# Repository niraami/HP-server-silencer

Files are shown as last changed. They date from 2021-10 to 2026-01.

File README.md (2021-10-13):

# HP server silencer

 

Inpired by the *many* other projects to silence the HP DL380e/p - but without most of the jank.  
Don't get me wrong, I love Arduino and projects that anyone can do themselves on a budget, but I just wanted something more robust. Something I could trust won't fail and somehow take the server with it. Something that is plug & play, and could be produced in bulk if needed (for relatively cheap).

I believe **this** is that something. The premise is quite simple. This STM32 equipped board acts as a middle man between the server & each fan. It takes the PWM signal from the server, scales & limits it to some user-configureable value and passes is along to the fan.

<div align="center">

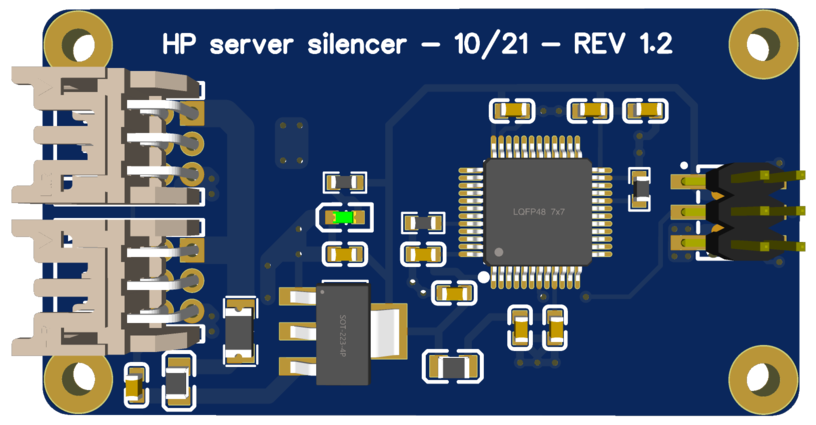
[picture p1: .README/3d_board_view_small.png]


</div>

# How it works
Here is a quick example of the boards fan curves in action. They are user configureable (i might even make a little configuration tool, so that you don't have to write configs manually.. if i feel motivated enough), but what you are seeing is the default curve that I've made as a good 'starting point'.  
I personally don't think it needs or should be changed, but I guess there are use cases where I can see both a *more* and *less* agressive curve make sense.

<div align="center">

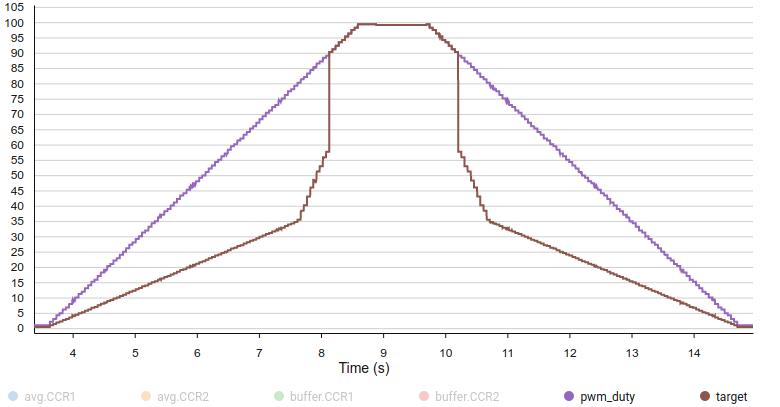
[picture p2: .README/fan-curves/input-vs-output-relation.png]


</div>

The **green curve is the input**. I've just got another STM32 producing a PWM signal @25kHz, that linearly sweeps the duty cycle from 0 to 100%, waits, and then back.  
The **red curve is the target** PWM. This is generated by the STM32 to control the fans.

Right now, you can manually configure the "fan curve" in [`curves.h`](src/Core/Src/curves.h).

Both of these values on the graph are after being smoothed/filtered via a rolling average. This average is produced by taking the last *n* samples (8 by default), or max. of last *t* milliseconds of data (400ms by default). What this means is that no data older than 400ms is taken into account for the average, and a maximum of last 8 values are.  
This technique gets rid of some of the signal uncertainty, but might not solve all of the issues that there are with scaling input values to different ranges - and also *maybe* introduces it's own artifacts, but none of those actually show up on my logic analyzer in a meaningful way, so it might just be issues with the STM32CubeMonitor polling rate or whatever.

Here are the values before any post processing is applied (on the left) and after (on the right).

<div align="center">

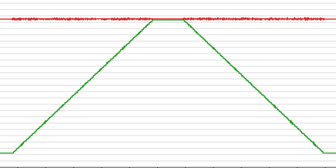
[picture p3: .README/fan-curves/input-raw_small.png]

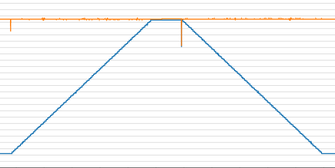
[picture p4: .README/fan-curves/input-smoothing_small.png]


</div>

# Design
All of the PCB design files can be found in the [pcb](pcb/) folder, but also on [OSHW](https://oshwlab.com/niraami/hp-server-silencer). 

I designed it from scratch in EasyEDA, and it has currently gone through 2 revisions. I've split them up using the EasyEDA versioning system, so you can check them out if, for whatever reason, you'd want...

The design is quite simple, as it just consists of 2 JST PHD 2.0 connectors, some power circuity, a STM32F103 (like in the bluepill) and a debugging header. All of the logic processing is done by the MCU, which is even more simplified by it's powerful PWM input & output capabilities. There are some quirks, but at least I didn't have to deal with counting the pulses myself or something.

To power the STM32, an AMS117-3.3 LDO piggibacks on the 12V coming from VCC - as the MCU requires literally milliamps of current, this shouldn't be an issue. I've chosen an LDO to simplify the programming & debugging, as it can also be powered off of 5V (from a USB port for example).

<div align="center">







</div>

## Fan PWM sense
The PWM Sense pins between the input & output connectors are connected - but it would be possible to reroute them, and use another STM32 timer to generate fake fan speed information for the server. The current server firmware version I've got doesn't seem to care about the reported speed much though, so I didn't implement that.

# Inspiration
Inspired by the many other HP fan "silencing" projects, but especially the [Max-Sum/HP-fan-proxy](https://github.com/Max-Sum/HP-fan-proxy) project. Though don't just blindly trust somebody's work, check it yourself... for example, I found that the the displayed [connector pinout](#motherboard-fan-pinout) doesn't match my server (and didn't check until the v1.0 of my board arrived :P).

These are just a *few* of the projects I came across while researching this topic. It seems that this series of server is quite notorious on [r/Homelab](https://www.reddit.com/r/homelab) for being so loud, people will try **literally** anything to make it shut up.
- [Silencing the HP Dl380, For Good.](https://www.reddit.com/r/homelab/comments/beuks5/silencing_the_hp_dl380_for_good/)
- [HP DL380p Arduino Fan Mod](https://www.reddit.com/r/homelab/comments/ny2eia/hp_dl380p_arduino_fan_mod_standby_question_and/)
- [Silence of the fans: Controlling HP server fans with a modified iLO4. And MORE!](https://www.reddit.com/r/homelab/comments/di3vrk/silence_of_the_fans_controlling_hp_server_fans/)
- [HP DL380P G8 fan noise with bios hack](https://www.reddit.com/r/homelab/comments/f94b0e/hp_dl380p_g8_fan_noise_with_bios_hack/)
- [Faking the fan signal on a DL380 G7](https://www.reddit.com/r/homelab/comments/72k3jf/faking_the_fan_signal_on_a_dl380_g7/)

# Sources
- [Max-Sum/HP-fan-proxy](https://github.com/Max-Sum/HP-fan-proxy)
- [STM32 Variable PWM Signal Output with timers, Keil Arm-mdk and Stm32cubemx ide](https://www.engineersgarage.com/stm32-variable-pwm-with-timers/)
- [Phil’s Lab - KiCad STM32 Hardware Design and JLCPCB Assembly](https://www.youtube.com/watch?v=t5phi3nT8OU)

# Part alternatives/not listed in BOM
- [50mm PHD2.0 JST cable (2x3P) - store 1](https://www.aliexpress.com/item/1005001346032672.html)
- [50mm PHD2.0 JST cable (2x3P) - store 2](https://www.aliexpress.com/item/1005002904897807.html)
- [JST PHD2.0 compatible 90˚ connector - alt 1](https://www.ebay.com/itm/PHD2-0-2-0mm-Pin-Header-PCB-Connector-Socket-Buckle-3-10P-Right-Angle-Various/153429645789)
- [JST PHD2.0 compatible 90˚ connector - alt 2](https://lcsc.com/product-detail/Wire-To-Board-Wire-To-Wire-Connector_HR-Joint-Tech-Elec-A2211WR-2X03P_C338851.html)
- [Tag-Connect - TC2030-IDC-NL-10](https://www.tag-connect.com/product/tc2030-idc-nl-10-6-pin-plug-of-nails-spring-pin-cable-with-0-1-ribbon-connector-10-version)
- [Tag-Connect - ARM20-CTX 20-Pin to TC2030-IDC Adapter for Cortex](https://www.tag-connect.com/product/arm20-ctx-20-pin-to-tc2030-idc-adapter-for-cortex)
- [USB connector to power the board while uploading firmware](https://www.aliexpress.com/item/4001198319430.html)

# Rants/stories

## Fan connectors
The connector type was very difficult to figure out, as it looks to be a proprietary 2.00mm pitch, 6 pin (2x3) keyed connector. And of course, HP will not just sell it to you, or even give you some datasheet for it.    
Luckily, Max's project was a very useful starting point, as Max found a compatible alternative, in the form of a JST PHD 2.0. Though, at first he wrote it to be a PH 2.0, but after much searching, I've found out that the D in PHD stands for "double row", and thus corrected him [here](https://github.com/Max-Sum/HP-fan-proxy/issues/4).

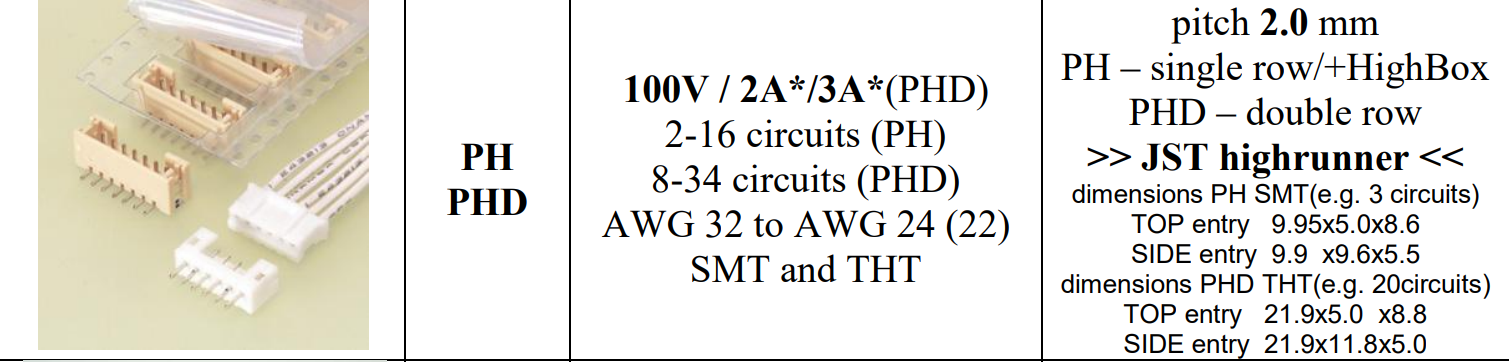
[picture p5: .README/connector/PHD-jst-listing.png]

The above screenshot is from a document which you can find [here](https://jst.de/uploads/product_overview/JST%20Product%20Overview_JD09.pdf) and a local copy at [docs/JST Product Overview_JD09.pdf](docs/JST%20Product%20Overview_JD09.pdf).

Not that just knowing the part number is going to do you much good.. it's a very rare one, barely anyone sells it, and crimping obscure JST's often requires special (and expensive) tools. But luck struck once again, and I managed to find a seller on AliExpress that has [super short PHD2.0](https://www.aliexpress.com/item/1005001346032672.html)'s in the 2x3 (6 pin) form!  
*In case that listing dissapears in the ether, here is at least the name:*  **5CM 26AWG 50MM PHD2.0 JST 2.0mm Pitch PHD PHDR-10VS 10 PIN Connector Wire Harness 2.0MM pitch 50MM double**

One more catch! I swear it's the last one ;)  
The connector doesn't fit into the header on the motherboard due to the small guides on the sides. But the plastic is soft enough, that with a steady hand and a sharp knife, they can be cut off really easily.

<div align="center">

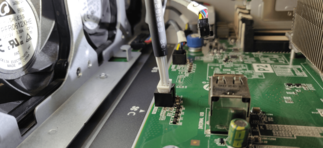
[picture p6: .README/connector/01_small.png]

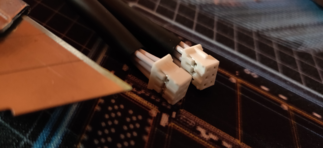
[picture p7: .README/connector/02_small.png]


</div>

## Motherboard fan pinout
Max's documentation provides a [very similar diagram](https://raw.githubusercontent.com/Max-Sum/HP-fan-proxy/master/images/post-8123-0-98784900-1394609613.png) to what I've got below, but we, for whatever reason, have the GND & NC pins swapped. There isn't even a cable there for me, so maybe there are some differences between server batches.. I've got no idea. So just in case, check what kind of a pinout your server has

Here is a "corrected" pinout, along with pictures of how the cable wires look (their colors do make a bit of sense):

<div align="center">

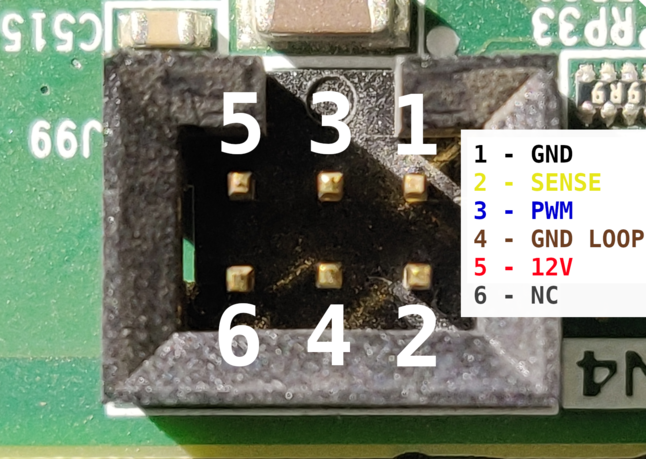
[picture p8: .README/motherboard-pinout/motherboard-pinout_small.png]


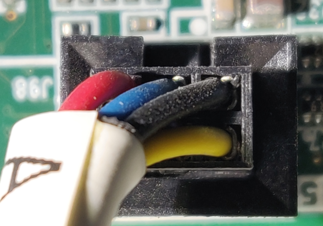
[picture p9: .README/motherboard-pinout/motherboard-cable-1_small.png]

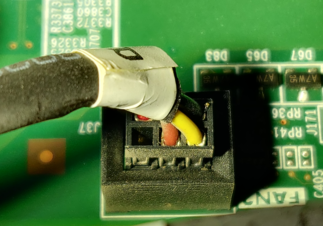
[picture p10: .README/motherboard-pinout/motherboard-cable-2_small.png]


</div>

## The server/fans use an inverted PWM signal
So yeah, I was very confused when plugging in my board that is meant to make the server more quiet, but instead it went full tilt. After a bit of headscratching, and using one of the prototype boards as a breakout, I figured out that what the ILO reports as 66%, is actually 33% duty cycle on the PWM.  
In STM32 terms, this is called PWM polarity, and should be set to `low`.

Luckily this required just 2 lines in the code to change, but nevertheless, it was quite funny.

<div align="center">

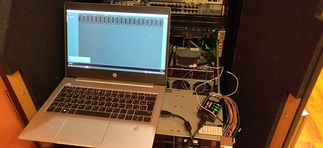
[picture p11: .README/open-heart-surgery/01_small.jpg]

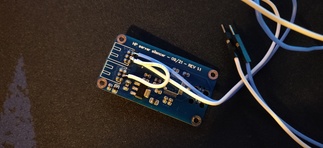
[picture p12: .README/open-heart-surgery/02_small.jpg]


</div>

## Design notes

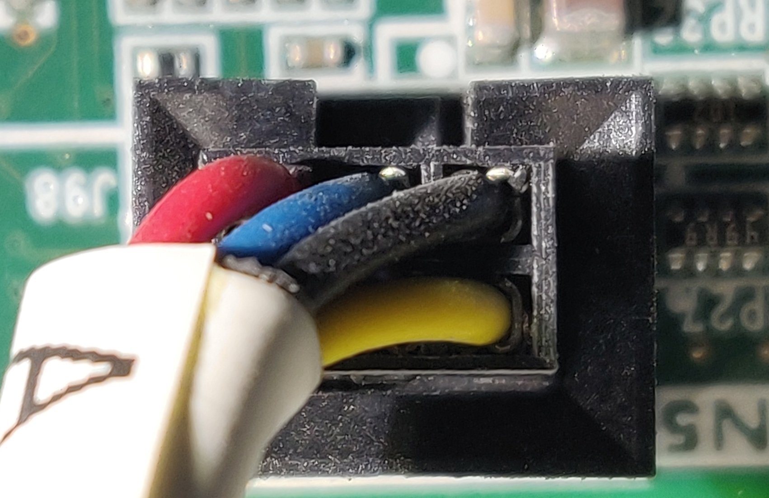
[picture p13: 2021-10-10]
.README/motherboard-pinout/motherboard-cable-1.png

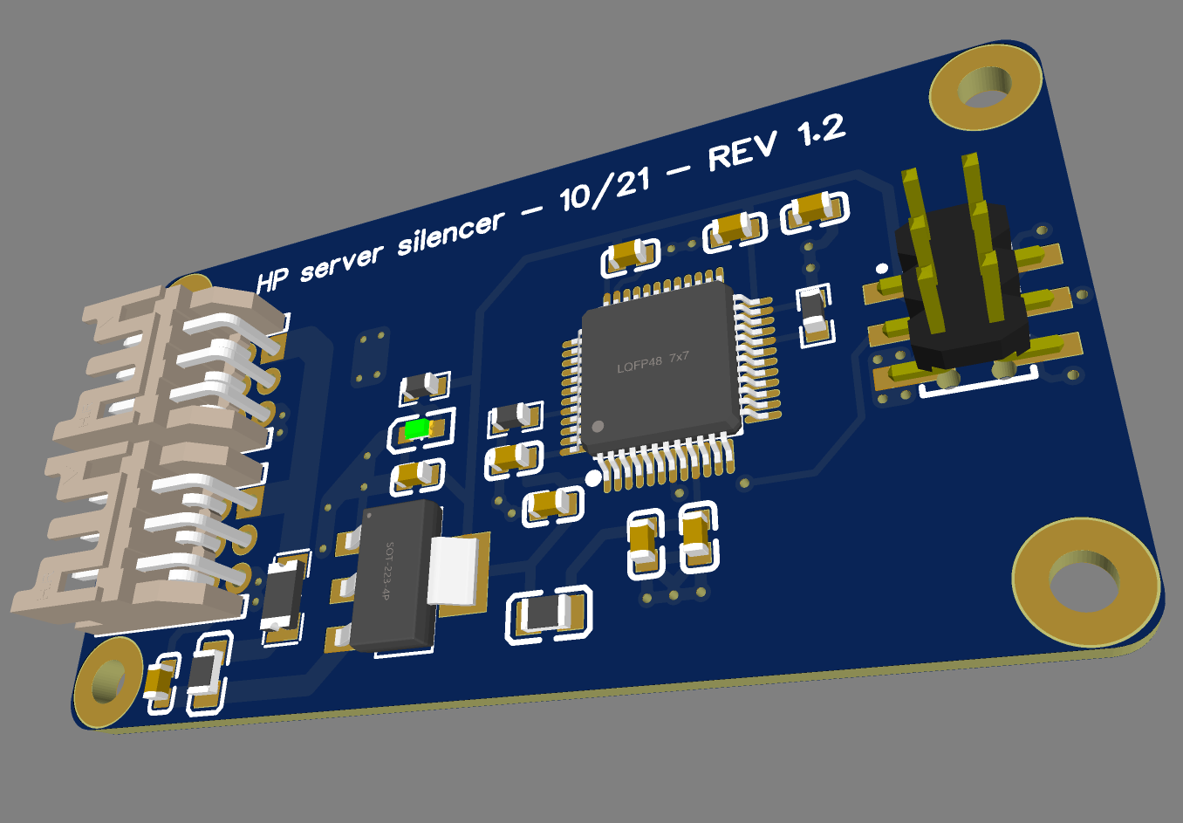
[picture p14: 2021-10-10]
.README/OSHW-thumbnail.png

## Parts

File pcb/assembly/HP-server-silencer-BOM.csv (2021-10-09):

ID | Name | Designator | Footprint | Quantity | Manufacturer Part | Manufacturer | Supplier | Supplier Part | Price
1 | TC2030-NL | P1 | TC2030-MCP-NL-JKA | 1
2 | PHD-2*3AW | J1,J2 | CONN-TH_A2004WR-2X03P | 2 | A2004WR-2X03P | HR(Joint Tech Elec) | LCSC | C476867 | 0.074
3 | STM32F103C8 | U3 | LQFP-48_L7.0-W7.0-P0.50-LS9.0-BL | 1 | STM32F103C8T6 | STMicroelectronics | LCSC | C8734 | 16.016
4 | SMD header | H1 | HDR-SMD_6P-P2.00-V-M-R2-C3-S2.0 | 1 | X4621WVS-2x03I-C40D64 | XKB Connectivity | LCSC | C917608 | 0.14
5 | Green | LED1 | LED0603-R-RD | 1 | 19-217/GHC-YR1S2/3T | EVERLIGHT | LCSC | C72043 | 0.025
6 | 180 | R3 | R0603 | 1 | 0603WAF1800T5E | UniOhm | LCSC | C22828 | 0.001
7 | 10uF | C1,C2,C12 | C0603 | 3 | CL10A106KP8NNNC | SAMSUNG | LCSC | C19702 | 0.007
8 | 350mA | F1 | F1206 | 1 | 1206L035YR | Littelfuse | LCSC | C99562 | 0.042
9 | 100 @ 100MHz | L1,L2 | L0805 | 2 | CBW201209U101T | FH | LCSC | C74487 | 0.005
10 | 10K | R1,R2 | R0603 | 2 | 0603WAF1002T5E | UniOhm | LCSC | C25804 | 0.001
11 | AMS1117-3.3 | U2 | SOT-223-3_L6.5-W3.4-P2.30-LS7.0-BR | 1 | AMS1117-3.3 | AMS | LCSC | C6186 | 0.17
12 | 100nF | C3,C5,C6,C7,C8 | C0603 | 5 | CC0603KRX7R9BB104 | YAGEO | LCSC | C14663 | 0.003
13 | 10nF | C4 | C0603 | 1 | 0603B103K500NT | FH(Guangdong Fenghua Advanced Tech) | LCSC | C57112 | 0.003

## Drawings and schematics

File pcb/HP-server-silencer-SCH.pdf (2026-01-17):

IO

## Power regulation

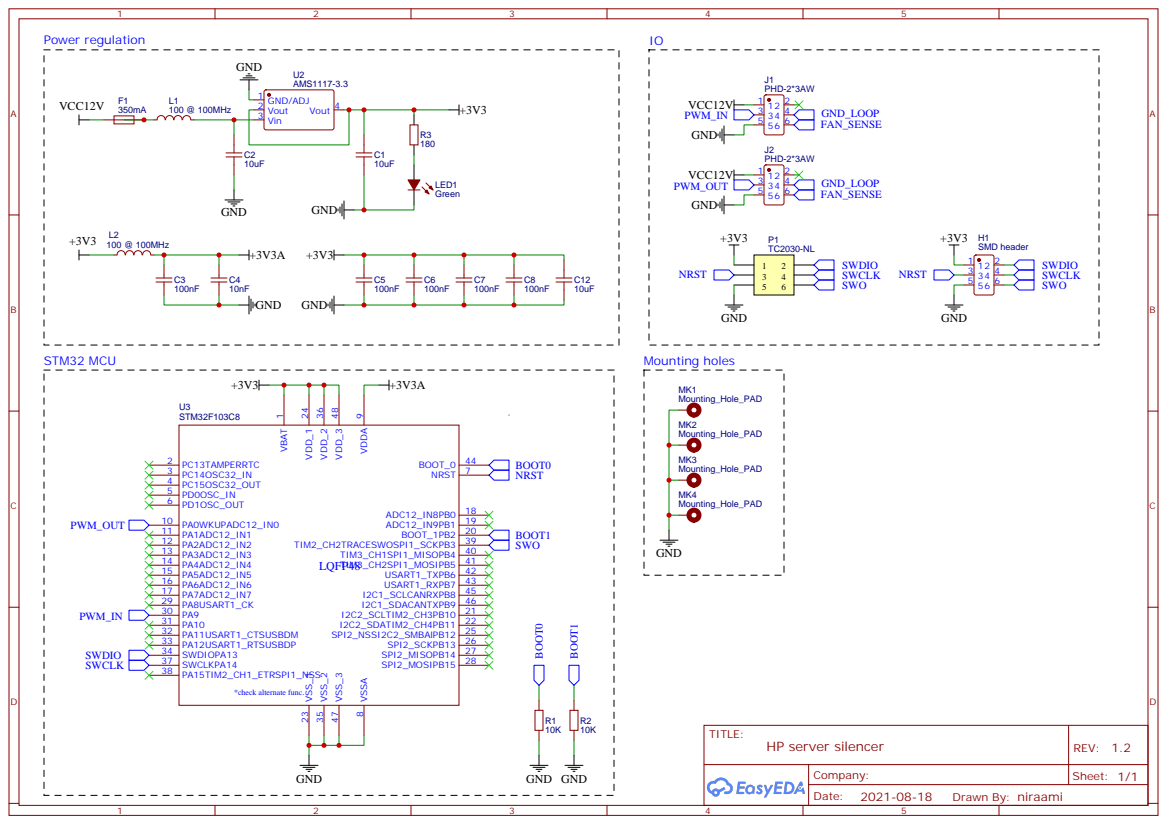
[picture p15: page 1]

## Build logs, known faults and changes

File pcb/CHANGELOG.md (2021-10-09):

(DD.MM.YYYY) - version

**19.08.2021 - v1.0**
Initial version

**11.09.2021 - v1.1**
*Complete redesign (of PCB, schematic mostly untouched)*
- input connectors are now on the same side to improve mounting in the server, as well as routing
- fixed completely incorrect input pinout
- fixed component spacing issues (gaps betwen caps were almost nonexistent)
- removed unnecessary silkscreen markings
- removed unnecessary decoupling caps
- replaced 3mm mounting holes /w 2mm

**07.10.2021 - v1.2**
*Minor fixes & improvements*
- fixed mirrored input connectors (GND flipped /w VCC, FAN_SENSE /w NC pin 2)
- replaced TC2050 /w TC2030-NL - less pins, no legs, etc
- added power indication LED
- added a SMD 2.5mm pitch pin header on top of the TC footprint (as an alternative)
- generally improved trace routing a bit (mostly optically & logically)

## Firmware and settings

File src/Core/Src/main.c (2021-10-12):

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
/* Includes ------------------------------------------------------------------*/
#include "main.h"
#include "cmsis_os.h"

/* USER CODE BEGIN Includes */
#include "curves.h"
/* USER CODE END Includes */

/* USER CODE BEGIN PD */

/**
 * Maximum number of messages that are pending from the TIM1 IRQ handler. This
 * buffer is used to handle bursts of messages from the IRQ - ex. when the PWM
 * signal is slowly changing.
 */
#define TIM1_IRQ_BUFFER_MAX_BACKLOG 4

/**
 * Maximum number of messages/events stored in the TIM1 IRQ buffer
 * This value directly affects how much smoothing is applied to the input signal
 * @note High values may lead to artifacts
 */
#define TIM1_IRQ_BUFFER_LENGTH 8

/**
 * Maximum lifespan of a buffer entry (in ms)
 * Specifies the maximum amount of time an entry is going to be counted into
 * the input average. After this time, the entry is guaranteed to be thrown
 * out. This might also happen much sooner if the interval at which the entries
 * are being added into the buffer is smaller than this value divided by the
 * buffer's length.
 * @note I recommend setting this value to be neatly divisible by the buffer's
 * length, otherwise rounding will take place anyways
 */
#define TIM1_IRQ_BUFFER_LIFESPAN 400

/**
 * This duty cycle is used on edge-cases where calculations fail or receive
 * invalid data
 * The default value is 100
 */
#define FAILSAFE_DUTY_CYCLE 100
/* USER CODE END PD */

TIM_HandleTypeDef htim1;
TIM_HandleTypeDef htim2;

/* Definitions for defaultTask */
osThreadId_t defaultTaskHandle;
const osThreadAttr_t defaultTask_attributes = {
  .name = "defaultTask",
  .stack_size = 128 * 4,
  .priority = (osPriority_t) osPriorityNormal1,
};
/* Definitions for inputFilter */
osThreadId_t inputFilterHandle;
const osThreadAttr_t inputFilter_attributes = {
  .name = "inputFilter",
  .stack_size = 128 * 4,
  .priority = (osPriority_t) osPriorityNormal,
};
/* USER CODE BEGIN PV */

/**
 * Message queue used to store reported CCR values from the TIM1_CC_IRQ handler
 */
MessageBufferHandle_t tim1_irq_backlog = NULL;
/**
 * A small buffer used to transfer the filtered signal from the input filter to
 * the main thread.
 */
MessageBufferHandle_t tim1_filtered_buffer = NULL;


/* USER CODE END PV */

void SystemClock_Config(void);
static void MX_GPIO_Init(void);
static void MX_TIM1_Init(void);
static void MX_TIM2_Init(void);
void StartDefaultTask(void *argument);
void InputFilterTask(void *argument);

/* USER CODE BEGIN 0 */

/**
 * @brief Sets the PWM duty cycle for the desired TIMER channel
 * @param htim Timer handle
 * @param channel PWM generation channel
 * @param duty_cycle Desired duty cycle in percent. Resolution is calculated
 * based on the period configured of the timer instance.
 */
static void setDutyCycle(TIM_HandleTypeDef* const htim,
    uint32_t channel, float duty_cycle)
{
  // Constrain the provided duty cycle to avoid undefined behaviour
  if (duty_cycle > 100) duty_cycle = 100;
  if (duty_cycle < 0) duty_cycle = 0;

  // Calculate the period resolution (1% of the period value)
  float pw_resolution = ((float)htim->Init.Period + 1.0f) / 100.0f;
  // Calculate & set the actual PWM period
  uint16_t pw_desired = pw_resolution * duty_cycle;
  __HAL_TIM_SET_COMPARE(htim, channel, pw_desired);
}

/* USER CODE END 0 */

/**
  * @brief  The application entry point.
  * @retval int
  */
int main(void)
{
  /* USER CODE BEGIN 1 */
  tim1_irq_backlog = xMessageBufferCreate(
    TIM1_IRQ_BUFFER_MAX_BACKLOG * (sizeof(CCRPair) + sizeof(size_t)) );
  tim1_filtered_buffer = xMessageBufferCreate(
    (sizeof(CCRPair) + sizeof(size_t)) );
  /**
   * Asserts will fail if there isn't sufficient FreeRTOS heap available for the
   * buffers to be created successfully.
   */
  assert_param(tim1_irq_backlog != NULL);
  assert_param(tim1_filtered_buffer != NULL);
  /* USER CODE END 1 */

  /* MCU Configuration--------------------------------------------------------*/

  /* Reset of all peripherals, Initializes the Flash interface and the Systick. */
  HAL_Init();

  /* Configure the system clock */
  SystemClock_Config();

  /* Initialize all configured peripherals */
  MX_GPIO_Init();
  MX_TIM1_Init();
  MX_TIM2_Init();
  /* USER CODE BEGIN 2 */

  // Start interrupts on TIM1 CH1 & CH2
  HAL_TIM_IC_Start_IT(&htim1, TIM_CHANNEL_1);
  HAL_TIM_IC_Start_IT(&htim1, TIM_CHANNEL_2);

  // Start PWM generation on TIM2 CH1
  HAL_TIM_PWM_Start(&htim2, TIM_CHANNEL_1);

  /**
   * Clear the TIM1 IRQ message queue, just in case anything got added during
   * initialization
   * @note This is mostly useful while using GDB for debugging
   */
  xMessageBufferReset(tim1_irq_backlog);

  /* USER CODE END 2 */

  /* Init scheduler */
  osKernelInitialize();

  /* USER CODE BEGIN RTOS_MUTEX */
  /* add mutexes, ... */
  /* USER CODE END RTOS_MUTEX */

  /* USER CODE BEGIN RTOS_SEMAPHORES */
  /* add semaphores, ... */
  /* USER CODE END RTOS_SEMAPHORES */

  /* USER CODE BEGIN RTOS_TIMERS */
  /* start timers, add new ones, ... */
  /* USER CODE END RTOS_TIMERS */

  /* USER CODE BEGIN RTOS_QUEUES */
  /* add queues, ... */
  /* USER CODE END RTOS_QUEUES */

  /* Create the thread(s) */
  /* creation of defaultTask */
  defaultTaskHandle = osThreadNew(StartDefaultTask, NULL, &defaultTask_attributes);

  /* creation of inputFilter */
  inputFilterHandle = osThreadNew(InputFilterTask, NULL, &inputFilter_attributes);

  /* USER CODE BEGIN RTOS_THREADS */
  /* add threads, ... */
  /* USER CODE END RTOS_THREADS */

  /* USER CODE BEGIN RTOS_EVENTS */
  /* add events, ... */
  /* USER CODE END RTOS_EVENTS */

  /* Start scheduler */
  osKernelStart();

  /* We should never get here as control is now taken by the scheduler */
  /* Infinite loop */
  /* USER CODE BEGIN WHILE */
  while (1)
  {
    /* USER CODE END WHILE */

    /* USER CODE BEGIN 3 */
  }
  /* USER CODE END 3 */
}

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
/* USER CODE BEGIN Header_StartDefaultTask */
/**
  * @brief  Function implementing the defaultTask thread.
  * @param  argument: Not used
  * @retval None
  */
/* USER CODE END Header_StartDefaultTask */
void StartDefaultTask(void *argument)
{
  /* USER CODE BEGIN 5 */
  CCRPair evt = { 0, 0 };

  /* Infinite loop */
  for(;;)
  {
    /** If > 0, we've received a message and it was stored to `evt` */
    size_t recv = xMessageBufferReceive(tim1_filtered_buffer,
      &evt, sizeof(evt), portMAX_DELAY);

    if (recv == 0) {
      // Continue waiting if the specified timeout expired
      continue;
    }

    /** Calculated input PWM frequency */
    uint32_t pwm_freq = HAL_RCC_GetSysClockFreq() / (TIM1->PSC + 1) / evt.CCR2;
    /** Ignore bogus input frequencies (outside of the PWM spec) */
    if (pwm_freq > 28000 || pwm_freq < 21000) {
      continue;
    }

    /** Calculated input PWM duty cycle as percentage */
    float pwm_duty = (evt.CCR2 - evt.CCR1) / (evt.CCR2 / 100.0f);
    // Invert the duty cycle, as it's polarity is reversed (low instead of high)
    pwm_duty = 100.0f - pwm_duty;

    // Find the first curve range that matches our input
    uint8_t n_curves = sizeof(k_curve) / sizeof(CurvePoint);

    for (uint8_t i = 0; i < n_curves; i++) {
      CurvePoint point = k_curve[i];

      if (point.in_start < pwm_duty && point.in_end > pwm_duty) {
        /** Target PWM duty cycle calculated based on the point's parameters */
        float target = point.out_start + (
          (point.out_end - point.out_start) * (pwm_duty - point.in_start) /
            (point.in_end - point.in_start)
        );

        setDutyCycle(&htim2, TIM_CHANNEL_1, target);

        break;
      }

      if (i + 1 == n_curves) {
        // Set failsafe duty cycle if no curve was found
        setDutyCycle(&htim2, TIM_CHANNEL_1, FAILSAFE_DUTY_CYCLE);
      }
    }
  }
  /* USER CODE END 5 */
}

/* USER CODE BEGIN Header_InputFilterTask */
/**
* @brief Function implementing the inputFilter thread.
* @param argument: Not used
* @retval None
*/
/* USER CODE END Header_InputFilterTask */
void InputFilterTask(void *argument)
{
  /* USER CODE BEGIN InputFilterTask */
  CCRPair data[TIM1_IRQ_BUFFER_LENGTH] = {0};
  CCRPair buffer = {0, 0};
  CCRPair sum = {0, 0};

  CCRPair* head_ptr = data;

  size_t recv = 0;
  size_t n_entries = 0;

  /** Used to optimize CPU cycles when no action is required */
  uint32_t cycle_ms = portMAX_DELAY;

  /* Infinite loop */
  for(;;)
  {
    // If > 0, we've received a message and it was stored to the buffer
    recv = xMessageBufferReceive(tim1_irq_backlog, &buffer,
      sizeof(CCRPair), cycle_ms);

    if (!recv && n_entries <= 1) {
      // Wait for a message indefinitely
      cycle_ms = portMAX_DELAY;

      continue;
    } else {
      cycle_ms = pdMS_TO_TICKS(
        TIM1_IRQ_BUFFER_LIFESPAN / TIM1_IRQ_BUFFER_LENGTH );
    }

    // Remove the entry that is about to get overwritten from the sum
    sum = (CCRPair) {
      sum.CCR1 - head_ptr->CCR1,
      sum.CCR2 - head_ptr->CCR2
    };

    if (!recv) {
      // Clear the current entry if no message was received
      *head_ptr = (CCRPair) {0, 0};
      // Decrement the number of available entries
      n_entries--;
    } else {
      // Append the new entry to the buffer & the rolling sum
      *head_ptr = buffer;

      sum = (CCRPair) {
        sum.CCR1 + head_ptr->CCR1,
        sum.CCR2 + head_ptr->CCR2
      };

      // Only increment the number of entries if the buffer isn't already full
      if (n_entries < TIM1_IRQ_BUFFER_LENGTH) {
        n_entries++;
      }
    }

    // Push the head_ptr address forward & check for bounds
    if (++head_ptr == &data[TIM1_IRQ_BUFFER_LENGTH]) {
      head_ptr = data;
    }

    // Send new input value to the main task
    CCRPair avg = {
      sum.CCR1 / n_entries,
      sum.CCR2 / n_entries
    };
    xMessageBufferSend(tim1_filtered_buffer, &avg, sizeof(CCRPair), 0);
  }
  /* USER CODE END InputFilterTask */
}

/**
  * @brief  Period elapsed callback in non blocking mode
  * @note   This function is called  when TIM4 interrupt took place, inside
  * HAL_TIM_IRQHandler(). It makes a direct call to HAL_IncTick() to increment
  * a global variable "uwTick" used as application time base.
  * @param  htim : TIM handle
  * @retval None
  */
void HAL_TIM_PeriodElapsedCallback(TIM_HandleTypeDef *htim)
{
  if (htim->Instance == TIM4) {
    HAL_IncTick();
  }
}

/**
  * @brief  This function is executed in case of error occurrence.
  * @retval None
  */
void Error_Handler(void)
{
  /* USER CODE BEGIN Error_Handler_Debug */
  /* User can add his own implementation to report the HAL error return state */
  __disable_irq();
  while (1)
  {
  }
  /* USER CODE END Error_Handler_Debug */
}

#ifdef  USE_FULL_ASSERT
/**
  * @brief  Reports the name of the source file and the source line number
  *         where the assert_param error has occurred.
  * @param  file: pointer to the source file name
  * @param  line: assert_param error line source number
  * @retval None
  */
void assert_failed(uint8_t *file, uint32_t line)
{
  /* USER CODE BEGIN 6 */
  /* User can add his own implementation to report the file name and line number,
     ex: printf("Wrong parameters value: file %s on line %d\r\n", file, line) */
  /* USER CODE END 6 */
}
#endif /* USE_FULL_ASSERT */

/************************ (C) COPYRIGHT STMicroelectronics *****END OF FILE****/

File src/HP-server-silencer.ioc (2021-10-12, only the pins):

Mcu.UserName=STM32F103C8Tx
PA0-WKUP.Signal=S_TIM2_CH1_ETR
PA13.Signal=SYS_JTMS-SWDIO
PA14.Signal=SYS_JTCK-SWCLK
PA9.Signal=S_TIM1_CH2
PB3.Signal=SYS_JTDO-TRACESWO

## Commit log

2021-08-20 Port project to STM32F103
2021-08-27 add: custom PCB files, rev 1.0
    [Gerber_BoardOutline.GKO, Gerber_BottomLayer.GBL, Gerber_BottomSilkLayer.GBO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]
2021-10-03 Switched internal clock to 32MHz to get 25KHz PWM
    16MHz could technically generate up to 80KHz /w 0.5% accuracy, but I
    wanted to generate exactly 25MHz with a nicely divisible number
    (256/2=128).
2021-10-03 Switched to CC interrupt & reimplemented duty code
    - switched from using the update NVIC to the capture compare NVIC
    - reimplemented capture callback code from master but changed it to use
    TIM1 CH2
2021-10-04 fix: PWM input duty cycle measurements
    - start interrupts on TIM1 CH1
    - change PWM input to combine channels 1 & 2
    - changed input period to 512 (to handle frequencies above 25KHz)
    [HP-server-silencer.ioc, main.c]
2021-10-07 Remove FreeRTOS
    Change of plans, no longer need or want an RTOS
    - i'm used to working with it, but it just doesn't work the same as it
    does on the ESP32, so it's annoying
    - realized that I won't actually need any threading support, as changes
    to the PWM variables are done in interrupts
    - debugging via GDB is quite a pain when a scheduler is constantly
    asking for attention
    [HP-server-silencer.ioc, main.c]
2021-10-07 Added PCB files for v1.2 of the board
    Added what is hopefully the final v1.x version of the board - I really
    really hope so cuz I just spent >150$ on a test batch...
    Also added a changelog & routing screenshots
    [Gerber_BoardOutline.GKO, Gerber_BottomLayer.GBL, Gerber_BottomSilkLayer.GBO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]
2021-10-07 fix: incorrect PWM output pin set
    Somehow while tweaking other stuff I've chosen the wrong PWM output pin
    (PA15 instead of PA0)... dunno how, but fixed
    [HP-server-silencer.ioc, main.c]
2021-10-08 Readded FreeRTOS, added PWM sweep demo
    After more testing, debugging & troubleshooting than you might even
    imagine, I've figured out why I had issues with the original code -
    essentially, you couldn't do pretty much anything inside of the TIM1 CC
    handler, as if you exceeded a certain runtime, the interrupts would
    start stacking and prevent the main thread from running.
    I've decided to resort to the FreeRTOS buffers as the fix. It also seems
    that the comments I made about difficult debugging and that I couldn't
    get it to work in the first place might've been a bit exagerrated.
    Debugging is harder due to the scheduler, yes, but breakpoints can help
    with that. And the 'getting it to work' part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
    [HP-server-silencer.ioc, main.c]
2021-10-08 fix: input prescaler scaled to work /w 64MHz
    [HP-server-silencer.ioc, main.c]
2021-10-08 Convert tabs to spaces, trim trailing whitespace
    Spaces are more universal, tabs can look in whatever way the person has
    their editor configured. Especially (i think) GitHub's default
    configuration is 4 spaces.
    2 spaces are superior.
    Fight me in the issues.
    [main.c]
2021-10-09 fix: reverse output PWM polarity
    Figured out that the HP server I've got uses reverse polarity PWM fans,
    so 90% is 10%, and 10% is 90%, etc
    Luckily this is a trivial thing to change on the STM!
    [HP-server-silencer.ioc, main.c]
2021-10-09 Implemented core functionality
    - solved the interrupt issues by moving the floating point calculations
    into the main thread and instead implementing a message buffer to
    notify that thread of changes in the PWM frequency/duty cycle changes
    - implemented a PWM curve structure to easily create linear scaling
    curves
    - implemented calculations for target PWM based on the scaling curve &
    the current input PWM signal's duty cycle
    -
    [main.c]
2021-10-09 fix: impl. failsafe when fan curves are missing
    [main.c]
2021-10-09 Dependency cleanup
    There were a lot of leftover files after merging the refactor branch, or
    maybe from switching to and from FreeRTOS a few times..
2021-10-10 Add documentation (README, more comments, etc)
    I've finally taken the time to write a (sort-of) proper project landing
    page & documentation.
    There are definitely parts I'd like to improve in the future, but I
    think that compared to other hobby projects out there, I've done an
    alright job.
2021-10-10 fix: invert input PWM, leftover files, readme
    - manually reversed polarity of the input PWM (as this cannot be done via the
    STM32 input configuration)
    - removed *-pos.csv file - this was an old CPL file, I've renamed and
    updated it since
    - fixed typos and stuff in README
    [HP-server-silencer-pos.csv]
2021-10-10 Documentation improvements
    - added the project thumbnail I used for OSHW/EasyEDA
    - added 2d board views
    - updated the curve to actually reflect the calculated input PWM (it was
    an issue with the way I was watching the variable, it wasn't actually
    jumping like that)
    - added abovementioned improvements to the README, along with some
    corrections and other improvements
    - added Design section to README
2021-10-12 add: input filtering
    - added input filter thread, that is responsible for actually receiving
    data (messages) from the CC IRQ
    - the main thread now receives filtered data that is the average of the
    last _n_ messages
    What I've essentially created is a rolling buffer, with one distinct
    feature. If no messages are received in the configured lifespan, the
    oldest messages are slowly removed from the queue & the sum/average is
    also updated to reflect that.
    This is to prevent cases where we stop receiving messages (stable or no
    PWM) essentially leaving whatever the last _n_ messages were in the
    buffer - as we want to reflect that the PWM has probably stabilized on
    the last received value.
    Hope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
    [HP-server-silencer.ioc, main.c]
2021-10-13 Readme & documentation improvements
    - added JST PHD2.0 listing & info
    - added parts section
    - scaled the 2D board view SVG's
    - scaled the board routing SVG's
2026-01-17 fix: replace incorrect PCB files
    [HP-server-silencer-schematic.schdoc]

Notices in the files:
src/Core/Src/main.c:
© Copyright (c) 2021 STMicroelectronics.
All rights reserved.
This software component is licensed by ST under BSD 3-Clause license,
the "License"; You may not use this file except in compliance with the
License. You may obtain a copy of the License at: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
